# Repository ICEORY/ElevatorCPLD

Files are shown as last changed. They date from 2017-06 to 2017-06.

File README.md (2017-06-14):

## **五层楼的简易电梯控制系统**

### 目录

[TOC]

### 整体方案设计

项目本着“各个击破，各司其职”的指导思想进行设计。各个击破是指将整个电梯控制系统分为各个小模块进行设计，在完成小模块设计之后再进行组合最终实现需要的功能；各司其职指在设计的时候保证每个小模块执行自己要实现的功能，能够正确处理设计范围内的输入。

将整个控制系统根据功能细分为各个小功能模块，主要利用JK触发器74113o以及8-3编码器74148、数值比较器7485等数字模块搭建出系统需要的各个小模块，最后根据各个模块的之间的逻辑联系构建出整个系统。

在使用QuartusII软件搭建各个模块时，每搭建一个功能模块就要对其输入输出逻辑进行仿真，保证其输入输出的波形图满足需要的逻辑功能。当每个模块都能各司其职时，最终搭建整个控制系统才能做到事半功倍，清晰有条理。

根据题目的设计要求，整个电梯控制系统结构图如下所示：

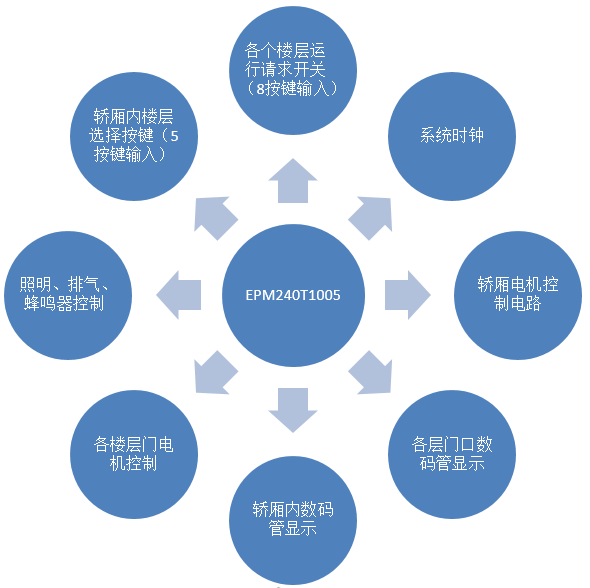
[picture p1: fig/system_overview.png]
system_overview


根据上述功能，将电路分为以下几个模块：

| 模块名称 | 目标实现功能 |
| --- | --- |
| keyinput | 获取单个按键输入，并能够存储按键状态，能够根据外部输入重置按键状态 |
| doormotor | 轿厢门电机，控制开关门动作，进行10ms计时，9s工作周期，其中开关门各一秒，停止7s，具有复位重新计时功能 |
| motion | 20s工作周期，能够根据上下行方向控制三相输出端的输出顺序 |
| timescale | 输入1KHZ时钟信号，进行分频之后输出1HZ,10HZ,100HZ,1KHZ的时钟信号 |
| floorcount  | 输入楼层到达信号时上升沿触发，根据运行方向进行所存储的楼层数的加减，并输出计算结果 |
| nextfloor | 根据运行方向上的按键信息判断是否需要继续运行，判断是否需要开门，判断下次运行方向 |
| otherdevice | 对电梯其他辅助模块如蜂鸣器、排气、照明等设备进行控制 |
| display | 轿厢内、电梯门口的电梯所在楼层信息显示，包括所在楼层，运行方向 |

电梯运行的逻辑如下所示：

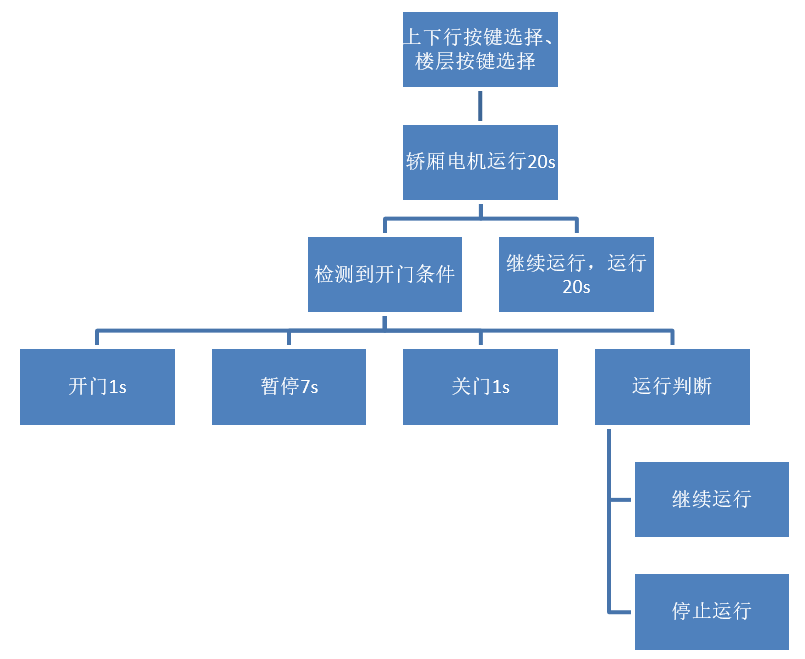
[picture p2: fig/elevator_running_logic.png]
elevator_running_logic


### 电路设计及原理说明

#### 按键电路设计

##### keyinput模块设计

根据功能要求，该模块的应具备以下的输入输出端口：

| input | output |
| ----- | --- |
| KEY | KEYSTATE |
| DONE  | DO |
| CLK | |

在逻辑上应满足：

1. 接收到外界按键信息时，将输出的KEYSTATE强制为1；
2. 当接收到复位指令DONE=1时，将KEYSTATE复位为0，并输入DO信号，用于指示其他模块执行任务；如：用于开门信号；

根据以上要求，使用JK触发器搭建该子模块,真值表如下：

KEYSTATE真值表：

| KEY  | DONE | KEYSTATE | KEYSTATE* |
| ---- | ---- | --- | --- |
| 0 | 0 | 0 | 0 |
| 0 | 0 | 1 | 1 |
| 0 | 1 | 0 | 0 |
| 0 | 1 | 1 | 0 |
| 1 | 0 | 0 | 1 |
| 1 | 0 | 1 | 1 |
| 1 | 1 | 0 | 1 |
| 1 | 1 | 1 | 1 |

DO真值表：

| DONE | KEYSTATE | DO | DO*  |
| ---- | --- | ---- | ---- |
| 0 | 0 | 0 | 0 |
| 0 | 0 | 1 | 0 |
| 0 | 1 | 0 | 0 |
| 0 | 1 | 1 | 0 |
| 1 | 0 | 0 | 0 |
| 1 | 0 | 1 | 1 |
| 1 | 1 | 0 | 1 |
| 1 | 1 | 1 | 1 |

根据计算得到的逻辑关系使用74113搭建出如下电路：

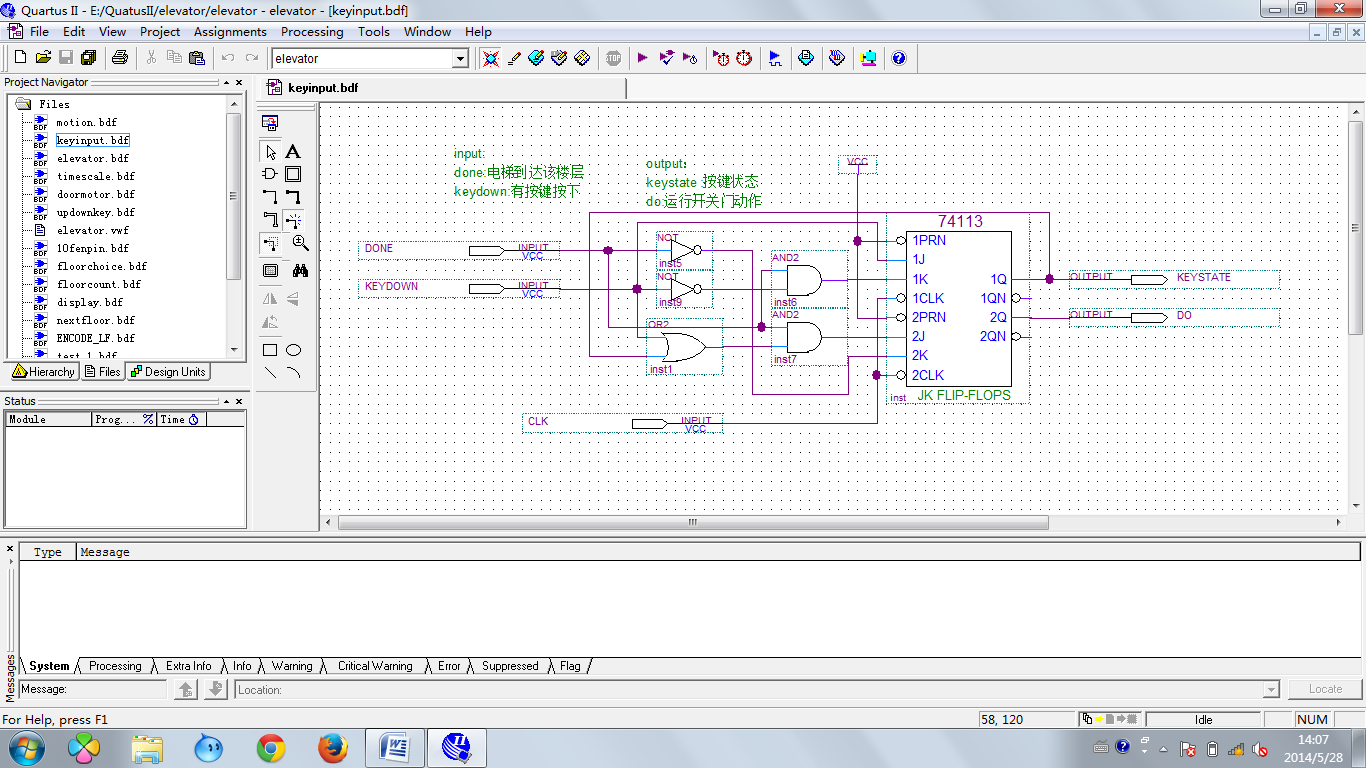
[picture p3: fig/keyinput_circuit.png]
keyinput_circuit


仿真结果如下所示：

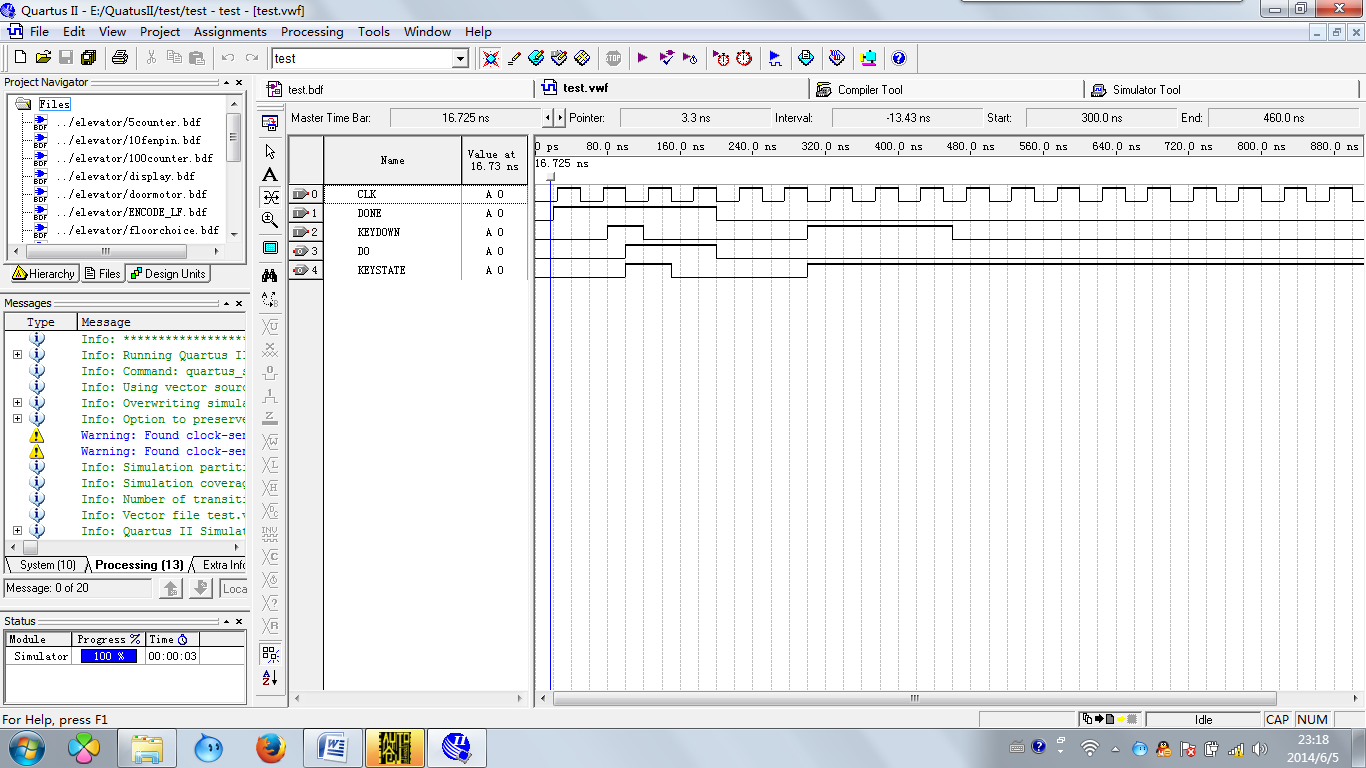
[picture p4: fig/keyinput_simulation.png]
keyinput_simulation


##### updownkey模块设计

构建完单个按键的输入电路之后利用该模块进一步构建电梯上下行选择按键输入；该模块由由八个keyinput单元构成；其输入输出如下表所示：

| input | output |
| --- | --- |
| UP1~UP4 | KEYSTATE1~KEYSTATE8 |
| DOWN2~DOWN5 | DOOR`~DOOR5 |
| CLK | |
| FLOORA~FLOORC | |
| U/D | |
| ARRIVE | |

根据五层电梯的实际情况，一楼只有上行按钮，五楼只有下行按钮，中间三层具有上下行按钮，共八个按键输入，输出控制五层楼的轿厢外门电机，故具有五个门控制输出，八个按键状态输出。

使用74138三-八译码器将输入的所在楼层信息译成八个按键状态的控制信息，其逻辑真值表如下：

| FLOORC | FLOORB | FLOORA | Y0 | Y1 | Y2 | Y3 | Y4 | Y5 | Y6 | Y7 |
| --- | --- | --- | ---- | ---- | ---- | ---- | ---- | ---- | ---- | ---- |
| 0 | 0 | 0 | 0 | 1 | 1 | 1 | 1 | 1 | 1 | 1 |
| 0 | 0 | 1 | 1 | 0 | 1 | 1 | 1 | 1 | 1 | 1 |
| 0 | 1 | 0 | 1 | 1 | 0 | 1 | 1 | 1 | 1 | 1 |
| 0 | 1 | 1 | 1 | 1 | 1 | 0 | 1 | 1 | 1 | 1 |
| 1 | 0 | 0 | 1 | 1 | 1 | 1 | 0 | 1 | 1 | 1 |
| 1 | 0 | 1 | 1 | 1 | 1 | 1 | 1 | 0 | 1 | 1 |
| 1 | 1 | 0 | 1 | 1 | 1 | 1 | 1 | 1 | 0 | 1 |
| 1 | 1 | 1 | 1 | 1 | 1 | 1 | 1 | 1 | 1 | 0 |

各个按键与输入的ARRIVE、U/D逻辑关系满足：（以Y2为例）

| ARRIVE | U/D  | Y2 | DONE |
| --- | ---- | ---- | ---- |
| 0 | 0 | 0 | 0 |
| 0 | 0 | 1 | 0 |
| 0 | 1 | 0 | 0 |
| 0 | 1 | 1 | 0 |
| 1 | 0 | 0 | 0 |
| 1 | 0 | 1 | 0 |
| 1 | 1 | 0 | 1 |
| 1 | 1 | 1 | 0 |

该模块的输出DOOR逻辑上等于各个按键子模块输出的DO

电路如下所示：

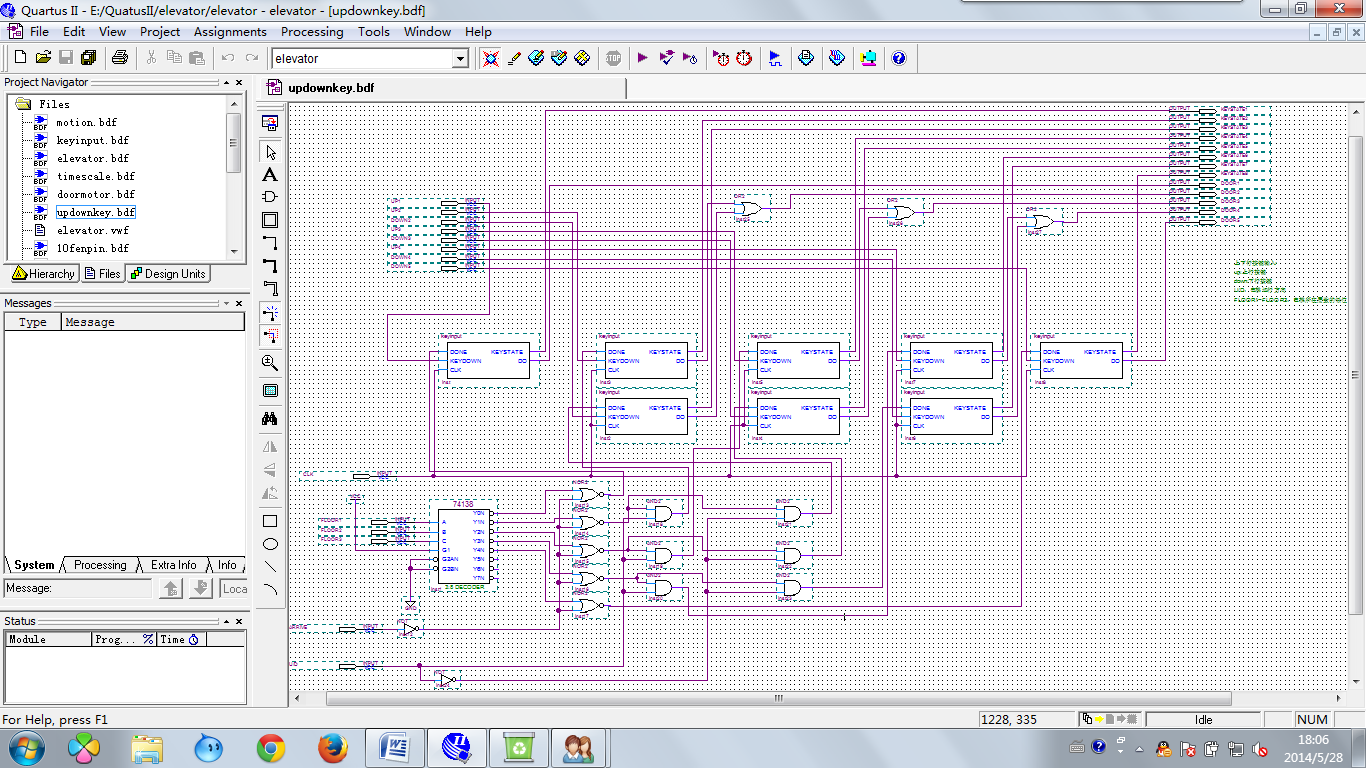
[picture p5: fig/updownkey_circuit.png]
updownkey_circuit


该模块整体仿真波形如下：

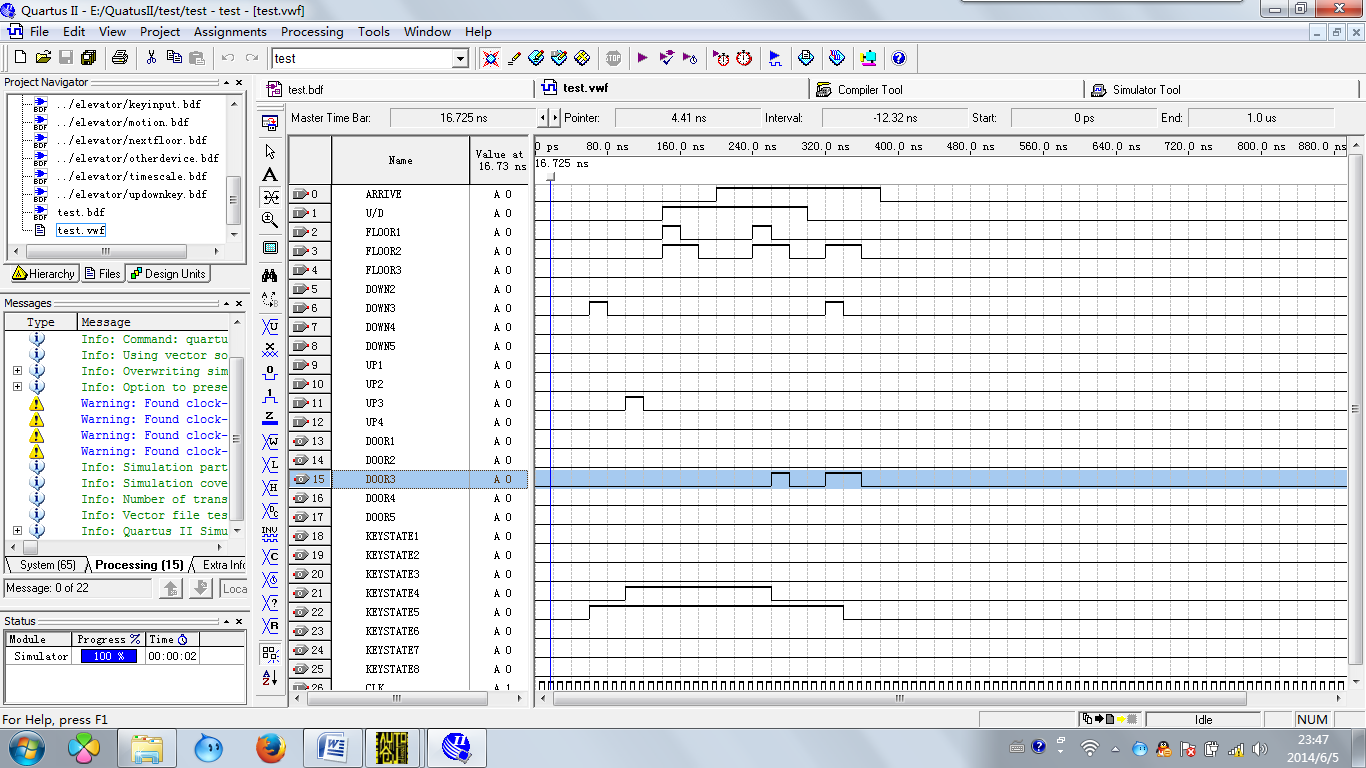
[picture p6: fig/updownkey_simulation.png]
updownkey_simulation


图中以第三层的上下行按键为例，在电梯没有到达三层时按下上下行按键，可见电梯不会进行开关门动作，并且将按键状态存储。在电梯到达三层时，由于电梯运行方向为上行（U/D=1），此时只判断上行方向的按键（KEYSTATE4），进行开门动作并将按键状态复位。电梯在三层的时候若运行方向改变为下行（U/D=0），此时进行开门动作，但由于同时在三层再次按下下行键故按键的按下状态一直持续到按键松开为止而，开门动作一直持续到楼层发生变化。可见，该模块设计符合实际电梯运行的逻辑。

##### floorchoice模块设计

电梯轿厢内的楼层选择仍选择用上述的按键模块，电路逻辑与updownkey模块的设计类似，其中keyinput模块满足：

1. KEYDOWN=KEY；
2. DONE=Y’ARRIVE’。

Floorchoice模块同时控制轿厢门电机的运动：

DOOR=DO1+D2+DO3+DO4+DO5;

电路设计如下所示：

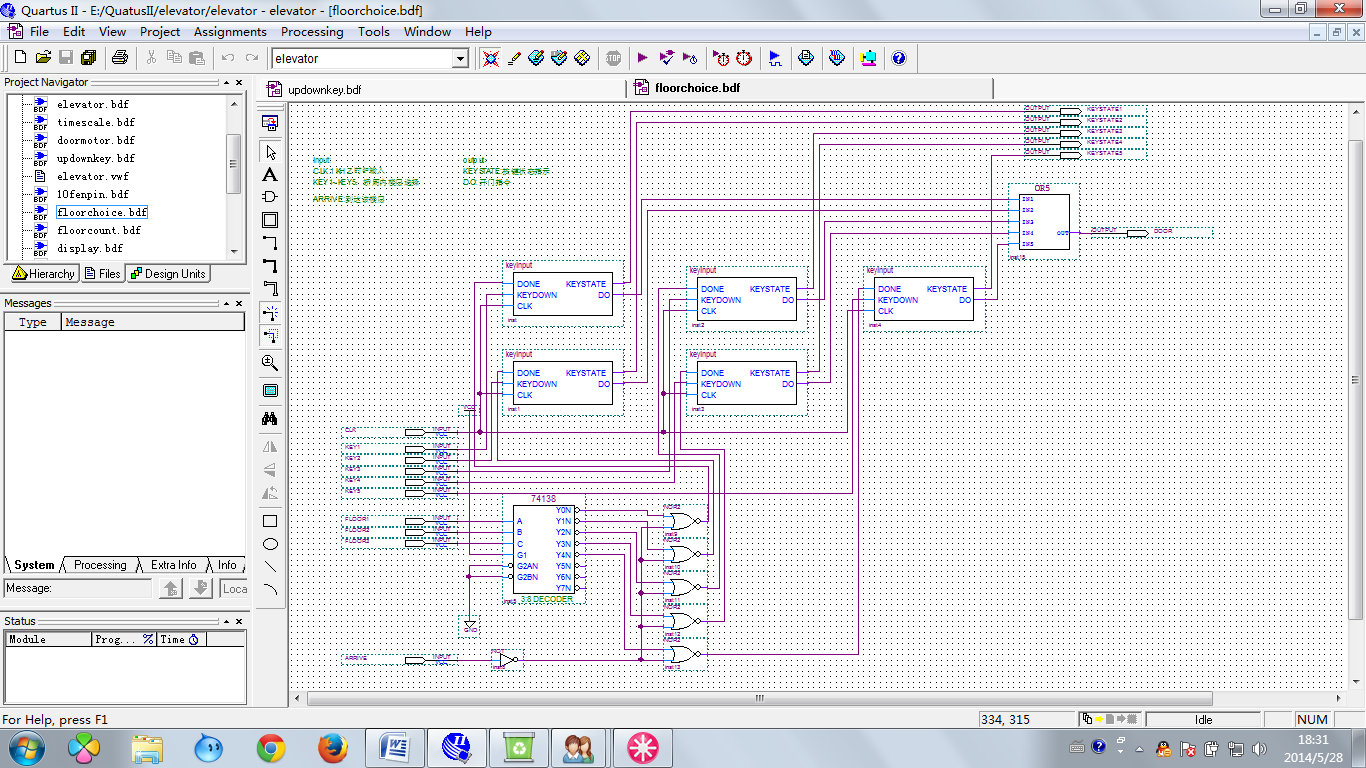
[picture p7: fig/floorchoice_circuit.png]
floorchoice_circuit


该模块整体仿真波形如下：

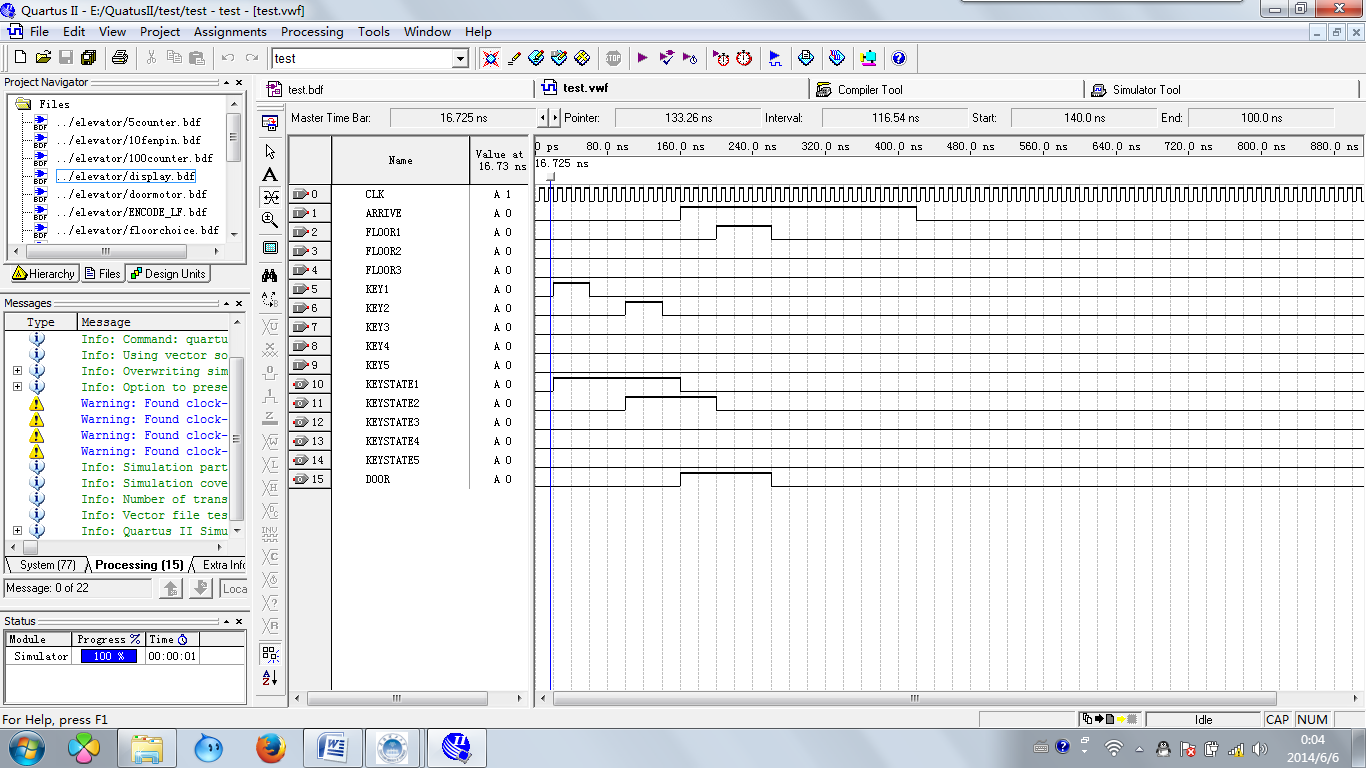
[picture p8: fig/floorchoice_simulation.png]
floorchoice_simulation


图中以一层与二层的按键选择为例，在电梯到达之前，根据输入将按键状态进行保存。在电梯到达相应楼层时进行开门动作并将对应按键复位。

#### 时钟电路设计

##### 10fenpin 模块设计

由于该电梯输入时钟频率为10kHz，故设计一个十分频电路将输入的时钟进行十分频，用于输出1Hz,10Hz,100Hz,1kHz等频率的时钟用于各个模块工作需要。使用74190十进制计数器作为分频核心模块，其逻辑真值表如下：

| QD | QC | QB | QA | CO |
| ---- | ---- | ---- | ---- | ---- |
| 0 | 0 | 0 | 0 | 0 |
| 0 | 0 | 0 | 1 | 0 |
| 0 | 0 | 1 | 0 | 0 |
| 0 | 0 | 1 | 1 | 0 |
| 0 | 1 | 0 | 0 | 0 |
| 0 | 1 | 0 | 1 | 1 |
| 0 | 1 | 1 | 0 | 1 |
| 0 | 1 | 1 | 1 | 1 |
| 1 | 0 | 0 | 0 | 1 |
| 1 | 0 | 0 | 1 | 1 |

电路设计如下所示：

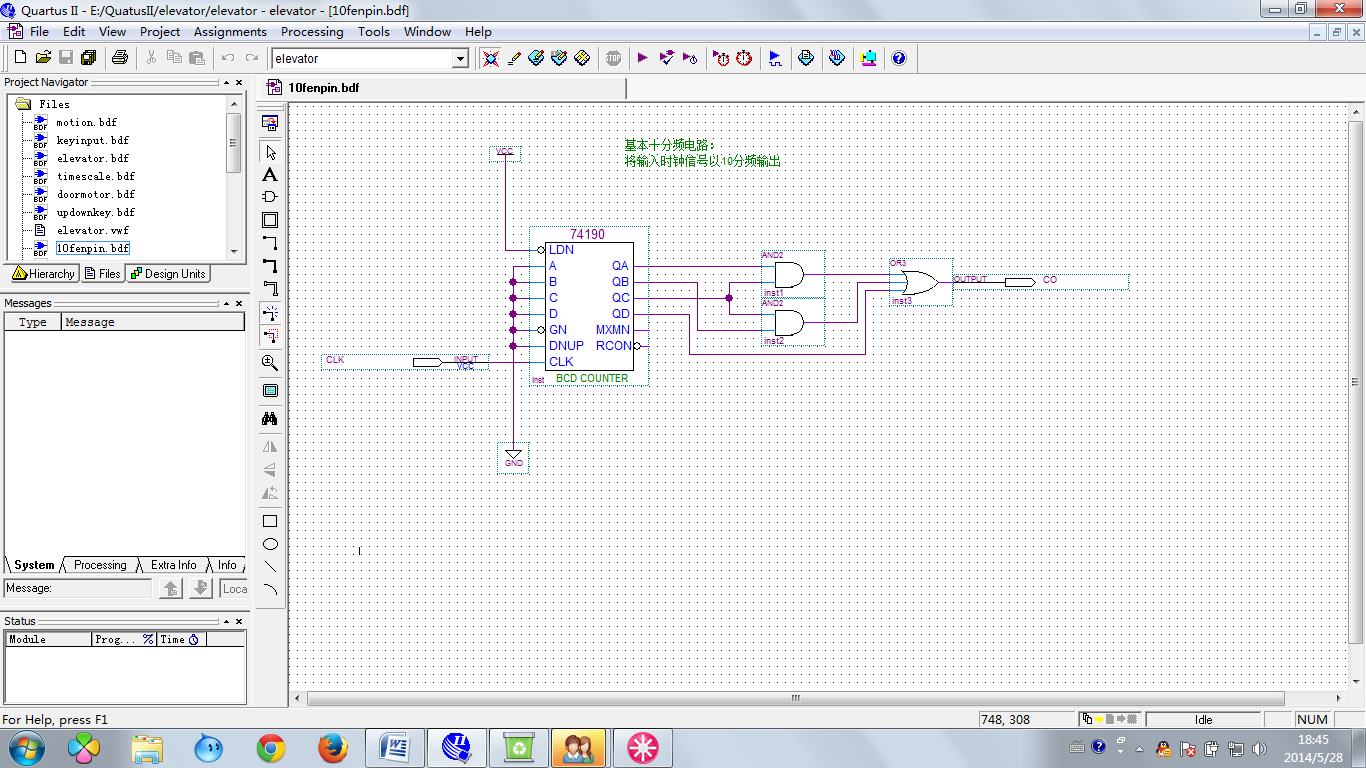
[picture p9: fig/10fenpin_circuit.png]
10fenpin_circuit


##### timescale模块设计

使用上述10fenpin模块构建多频率输出的timescale模块用于提供各个模块的时钟信号。模块原理同异步计数器的设计原理，电路图如下所示：

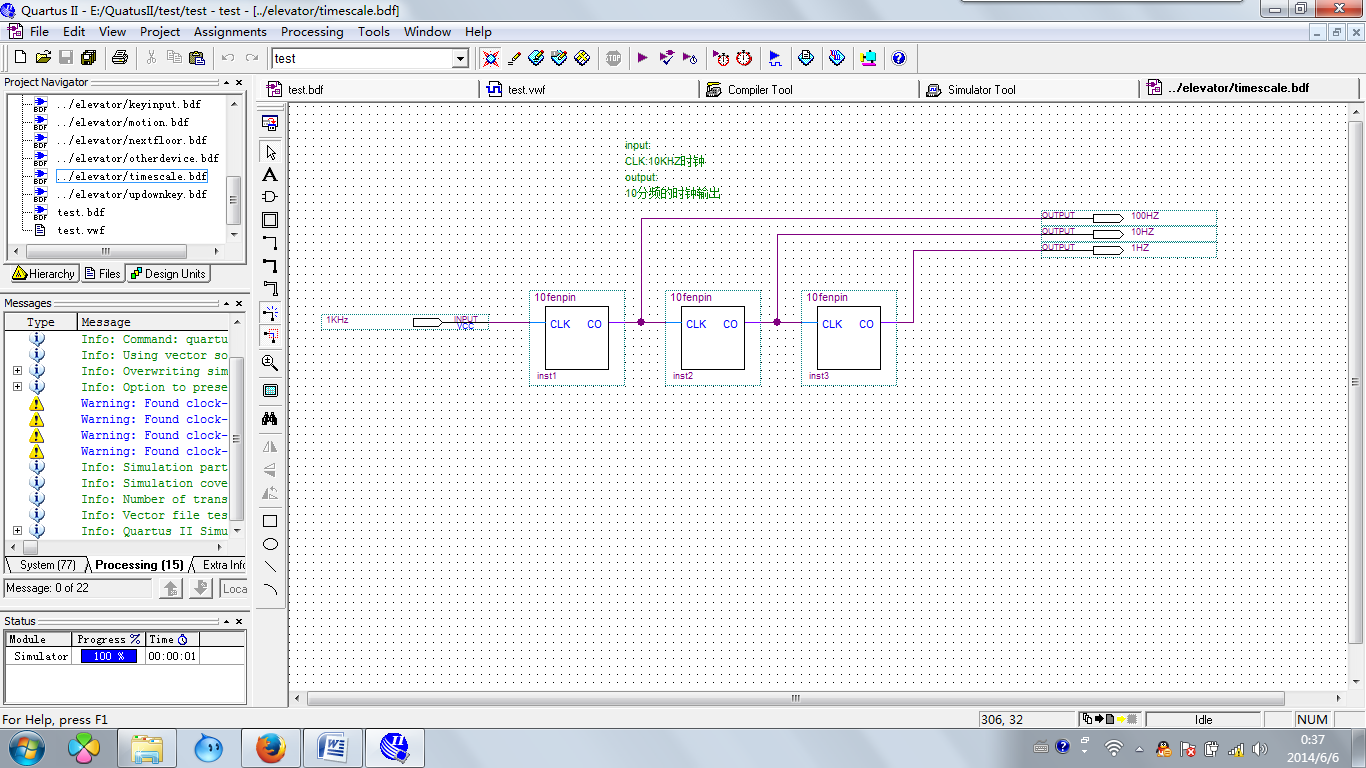
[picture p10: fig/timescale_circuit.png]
timescale_circuit


#### 系统决策电路设计

##### ENCODE_LE模块设计

由于8-三编码器74148是高位优先编码器，根据电梯上下楼层排序的需要，在下行时需要对输入进行低位优先编码，故以编码器74148为核心设计一个五-三低位优先编码器；设计原理是先将输入进行倒序处理,模块输入与74148芯片接口如下：

| IN4  | 0N |
| ---- | ---- |
| IN3  | 1N |
| IN2  | 2N |
| IN1  | 3N |
| IN0  | 4N |

根据上表可以对输入的低位进行优先编码，但由此导致了输出与输入的错位，使用门电路对输出进行校正，使输入IN0=1时，输出编码A2=0;A1=0;A3=0;真值表如下所示：

| A2N  | A1N  | A0N  | A2 | A1 | A0 |
| ---- | ---- | ---- | ---- | ---- | ---- |
| 1 | 1 | 1 | 1 | 0 | 0 |
| 1 | 1 | 0 | 0 | 1 | 1 |
| 1 | 0 | 1 | 0 | 1 | 0 |
| 1 | 0 | 0 | 0 | 0 | 1 |
| 0 | 1 | 1 | 0 | 0 | 0 |

此外当外界没有输入时，A2=1，A1=1;A0=1;

电路设计如下所示：

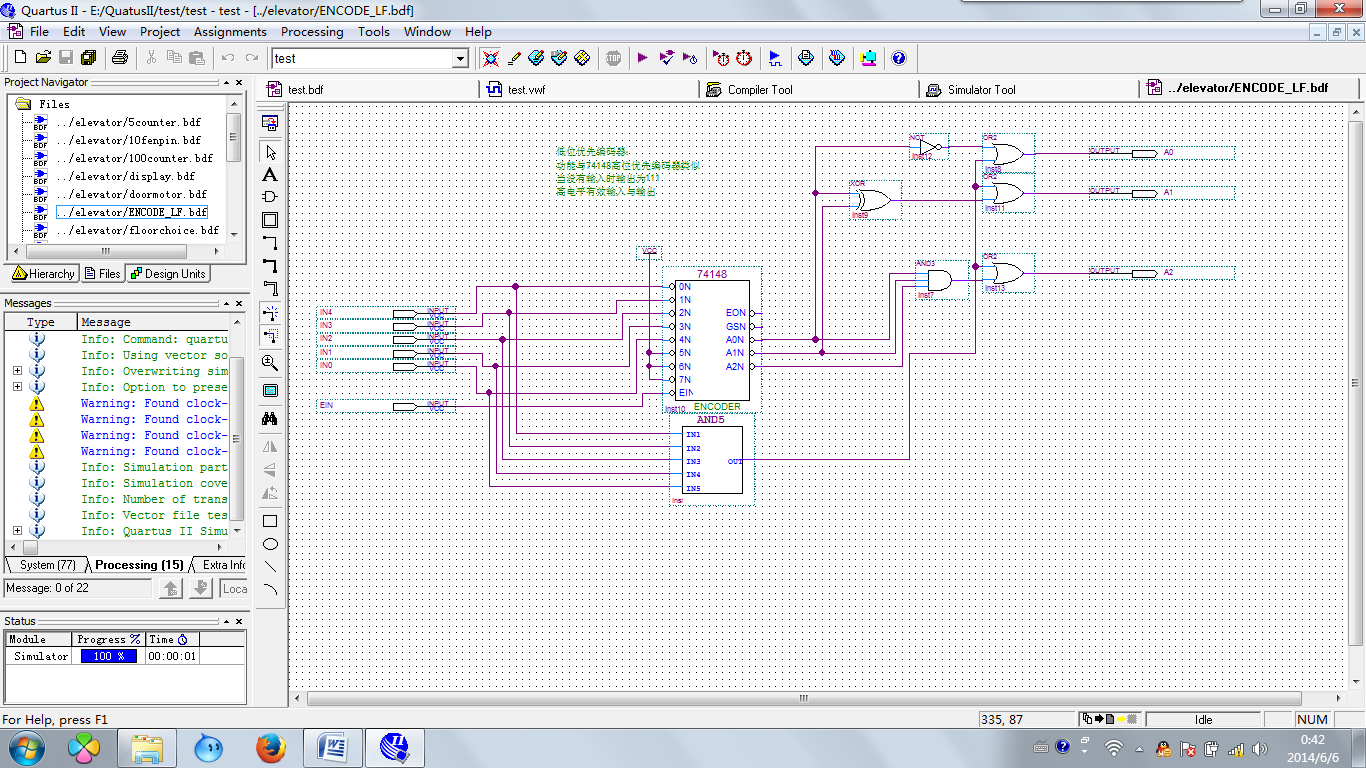
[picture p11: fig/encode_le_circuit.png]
encode_le_circuit


仿真波形如下图所示：

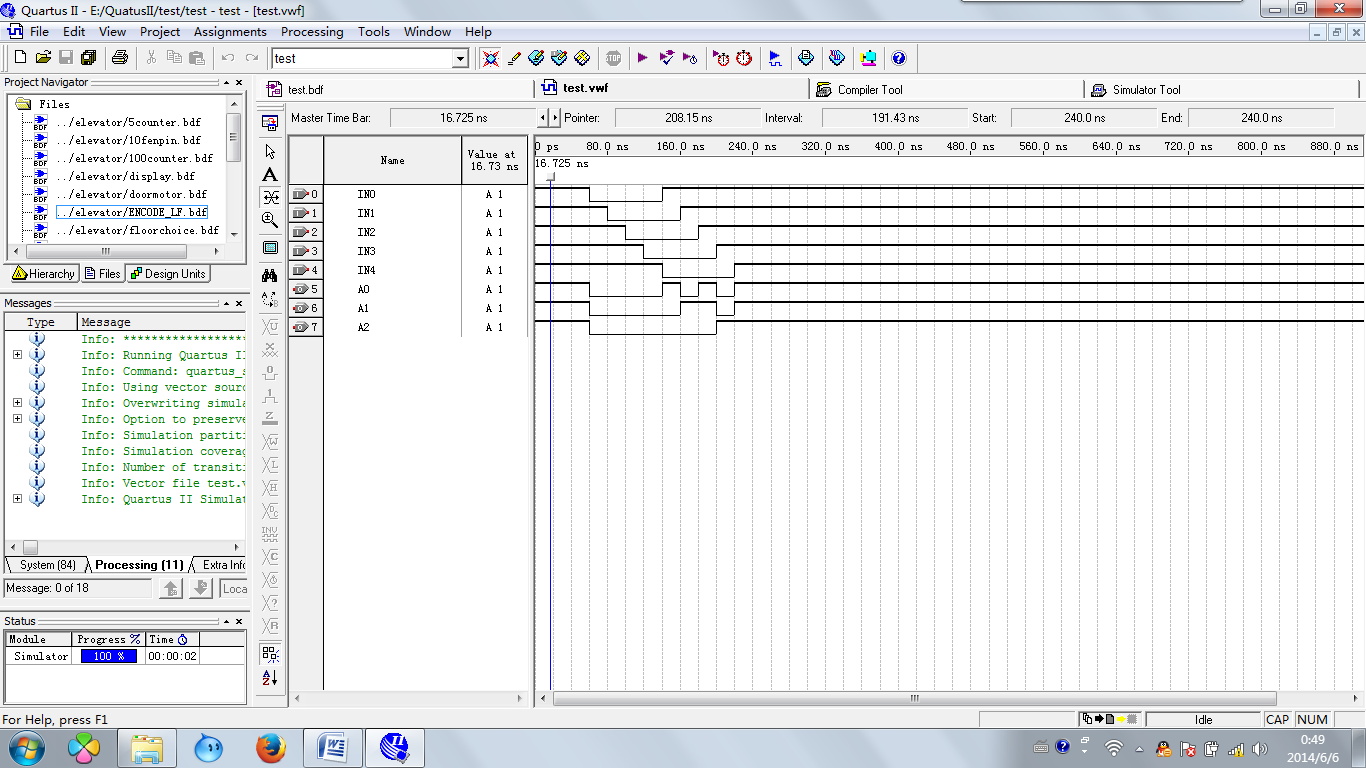
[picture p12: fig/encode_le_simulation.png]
encode_le_simulation


##### nextfloor模块设计

使用上述构建的ENCODE_LF模块与高位优先编码器74148搭建电梯的核心决策模块nextfloor，该模块根据按键的输入以及当前电梯所在的楼层输出电梯即将进行的动作，输入输出列表如下：

| KEYSTATE1~KEYSTATE8(上下行按键选择) | OPEN（开门信号）  |
| --- | --- |
| CHOICE1~CHOICE5（目标楼层选择） | RUN（电梯运行信号） |
| FLOORA~FLOORC（当前电梯的位置） | DIR（电梯运行方向） |
| CLK | |

使用高位优先编码器对输入的KEYSTATE以及CHOICE进行高位优先编码，输出其中的按键的最大值并使用数值比较器7485将键值与当前电梯所处的楼层进行比较决定电梯是否继续运行，设U=1表示电梯上行方向上有按键按下，且键值大于当前楼层；U=0 表示电梯上行方向没有键值大于当前楼层的按键按下；设D=1 表示电梯下行方向有键值小于当前楼层的按键按下；D=0表示电梯下行方向没有键值小于当前楼层的按键按下；电梯是否继续运行的判断值RUN应该满足RUN=U+D;

而电梯运行的方向DIR与U/D关系的真值表如下：

| U | D | DIR  | DIR* |
| ---- | ---- | ---- | ---- |
| 0 | 0 | 0 | X |
| 0 | 0 | 1 | X |
| 0 | 1 | 0 | 0 |
| 0 | 1 | 1 | 0 |
| 1 | 0 | 0 | 1 |
| 1 | 0 | 1 | 1 |
| 1 | 1 | 0 | 0 |
| 1 | 1 | 1 | 1 |

当U/D均为0时需要对电梯的运行方向进行进一步的判断，U/D为零一般出现在第一次按下上下行按键时出现，此时电梯位置与按键所在楼层一致且没有其他按键按下，故设UE=1表示电梯所在位置有上行方向的按键按下且没有其他按键选择；DE=1表示电梯所在位置有下行方向的按键按下且没有其他按键选择；

此时RUN=0,DIR与UE/DE的关系如下：

| UE | DE | DIR  | DIR* |
| ---- | ---- | ---- | ---- |
| 0 | 0 | 0 | 0 |
| 0 | 0 | 1 | 1 |
| 0 | 1 | 0 | 0 |
| 0 | 1 | 1 | 0 |
| 1 | 0 | 0 | 1 |
| 1 | 0 | 1 | 1 |
| 1 | 1 | 0 | 0 |
| 1 | 1 | 1 | 1 |

开门信号OPEN=RUN’DE

电路设计如下图所示：

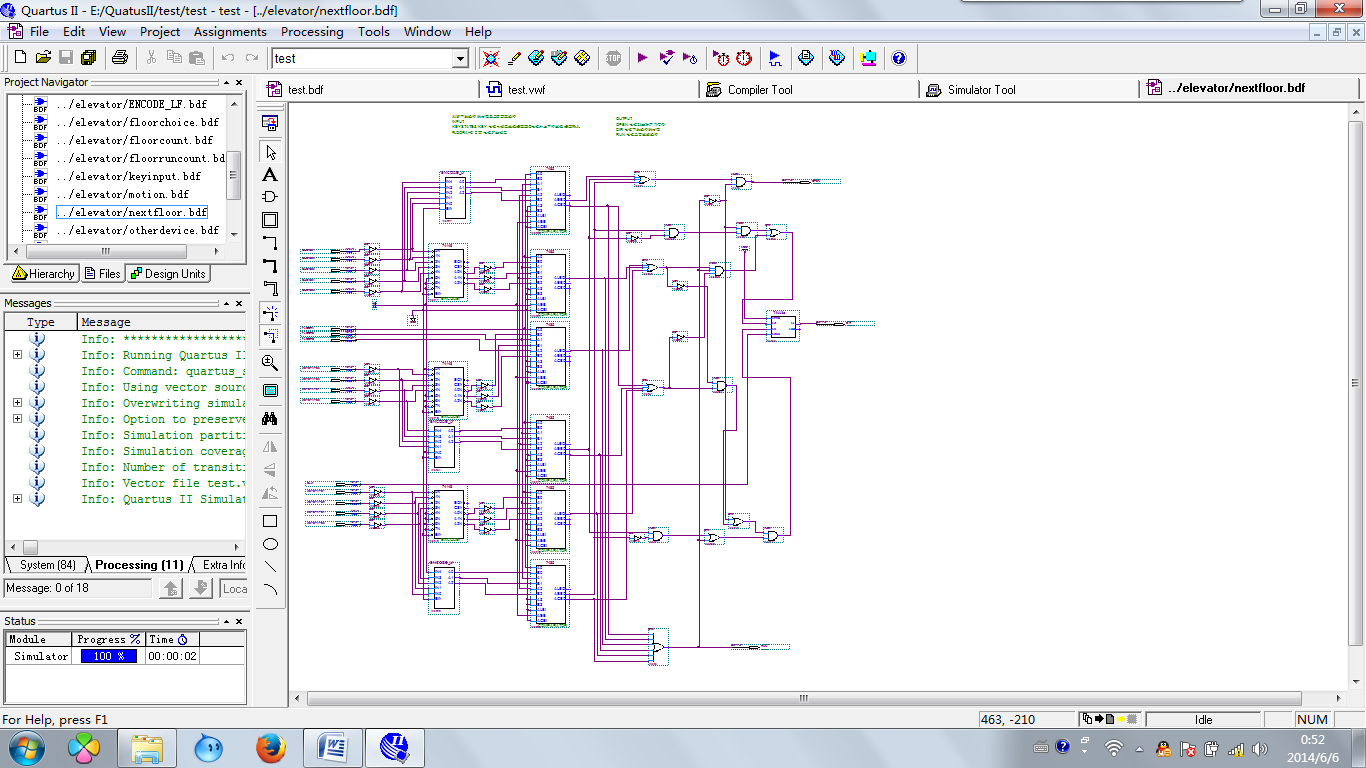
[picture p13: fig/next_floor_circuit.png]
next_floor_circuit


#### 电机电路设计

##### motion模块设计

由于本课题所使用的轿厢电机设定为四线三相步进电机，故需要根据输入的运行方向以及开门信号输出相应的三相电压的变化，电机正转时运行逻辑为A-B-C-A,反转时逻辑为A-C-B-A。使用双JK触发器74113构建三进制触发器，其计数顺序为00-01-10-00。

Q2\*Q1\*的卡诺图如下所示：

| Q2  Q1 | 0 | 1 |
| --- | ---- | ---- |
| 0 | 01 | 10 |
| 1 | 00 | XX |

    电机控制输出的逻辑真值表如下所示：

| RUN  | U/D  | Q2Q1 | A | B | C |
| ---- | ---- | ---- | ---- | ---- | ---- |
| 0 | X | X | 0 | 0 | 0 |
| 1 | 0 | 00 | 1 | 0 | 0 |
| 1 | 0 | 01 | 0 | 1 | 0 |
| 1 | 0 | 11 | 0 | 0 | 1 |
| 1 | 1 | 00 | 1 | 0 | 0 |
| 1 | 1 | 01 | 0 | 0 | 1 |
| 1 | 1 | 10 | 0 | 1 | 0 |

此外根据题目要求，每两个楼层之间电机运行时间为20s，故使用十进制计数器74190与二进制计数器74161构成二十进制计数器。

电路设计如下所示：

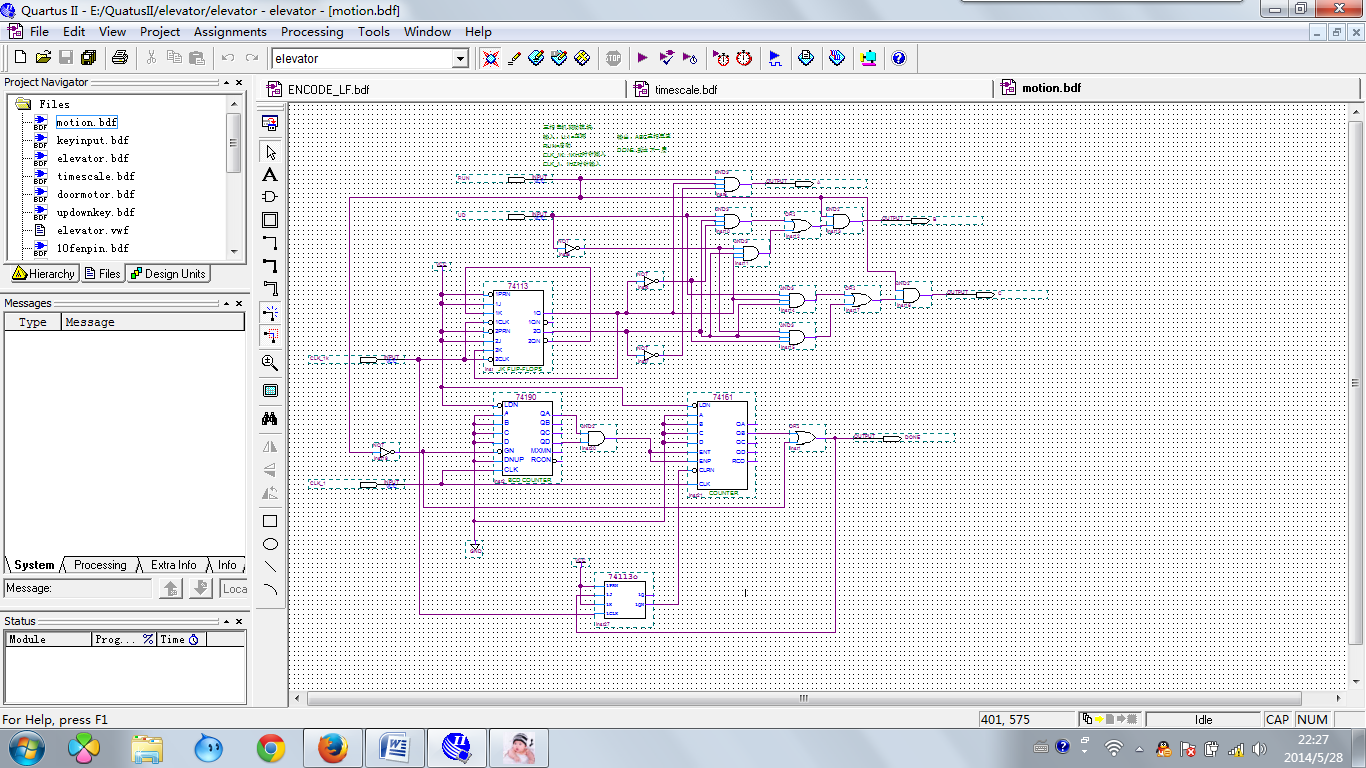
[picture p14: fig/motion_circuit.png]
motion_circuit


##### doormotor模块设计

在电梯到达目标楼层之后，电梯需要控制门电机依次执行以下动作：开门1s—停止7s—关门1s；其中在关门1s时间内根据电梯实际运行方向判断相应的按键输入，如上行时上行按键按下或者下行时下行按键按下则门重新打开，或者在门关闭时遇到障碍物也重新打开门。由分析可知，以上三种门重新打开的情况只需要归结为一个复位开门的指令给门电机控制模块即可。

由于本课题的门电机选择直流电机，故只需要输出MOTOR1/MOTOR2控制电机的正反转。使用三个74161十六进制计数器搭建900进制计数器，输入100Hz时钟信号控制。在0s时启动MOTOR1，关闭MOTOR2，此时直流电机正转，在1s时关闭MOTOR1，同时保持MOTOR2关闭，此时直流电机不转，在8s时保持MOTOR1关闭，启动MOTOR2，此时直流电机反转，9s时关闭MOTOR2，同时输出电机关门完成信号。****

电路逻辑真值表如下：

| RUN  | Q9~Q0 | MOTOR2  MOTOR1 | DONE |
| ---- | --- | --- | ---- |
| 0 | XXXXXXXXXX | 00 | 1 |
| 1 | 0000000000 | 01 | 0 |
| 1 | 0001100100 | 00 | 0 |
| 1 | 1100100000 | 10 | 0 |
| 1 | 1110000100 | 00 | 1 |

电机运行复位，即计数清零端CLRN’真值表如下：

| RUN  | MOTOR2 | RESET | CLRN |
| ---- | --- | ----- | ---- |
| 0 | X | X | 0 |
| 1 | 0 | X | 1 |
| 1 | 1 | 0 | 1 |
| 1 | 1 | 1 | 0 |

则电路设计如下图所示：

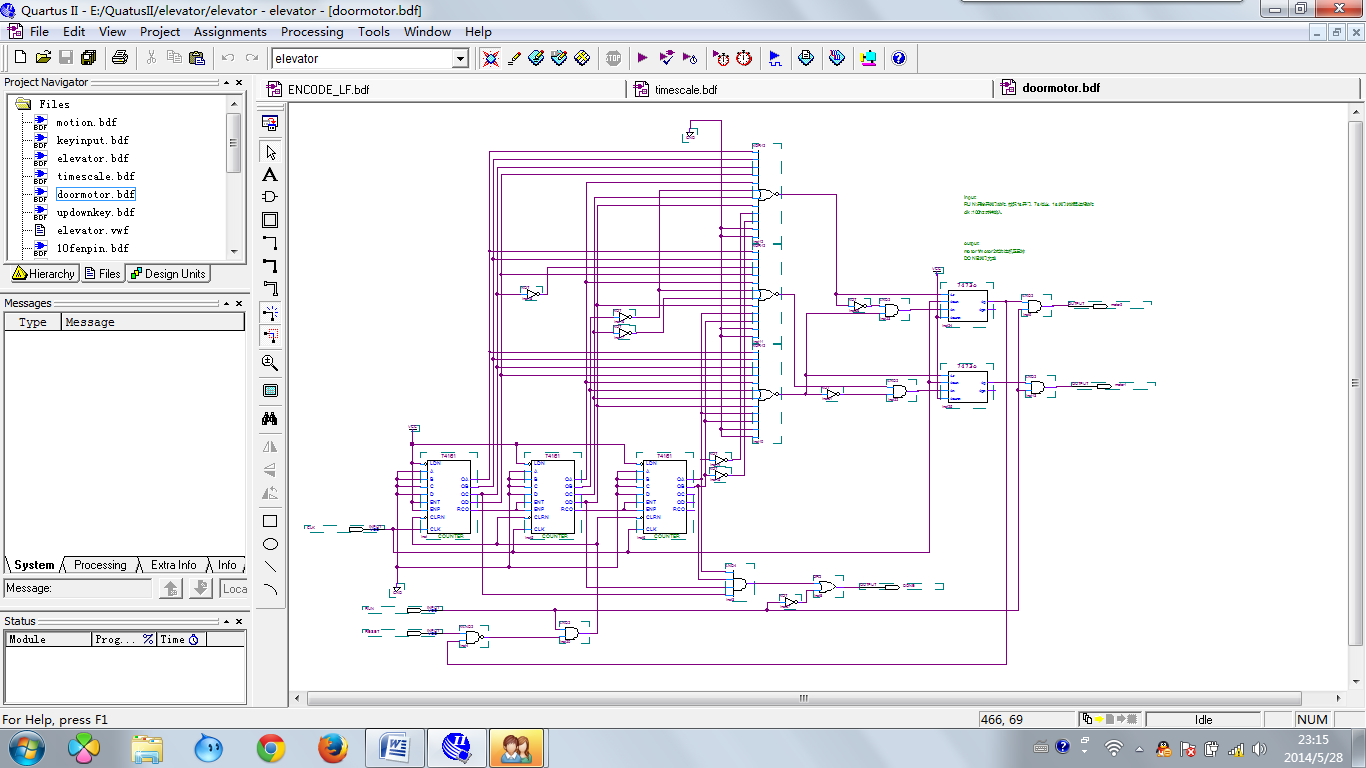
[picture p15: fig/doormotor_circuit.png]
doormotor_circuit


#### 楼层计数电路设计

##### 100counter模块设计

根据题目要求需要对各个楼层进行运行次数计数，考虑到运行次数可能比较多，故采用100进制计数模块，该模块是由两个74190十进制计数器构成的异步计数器，电路原理图如下所示：

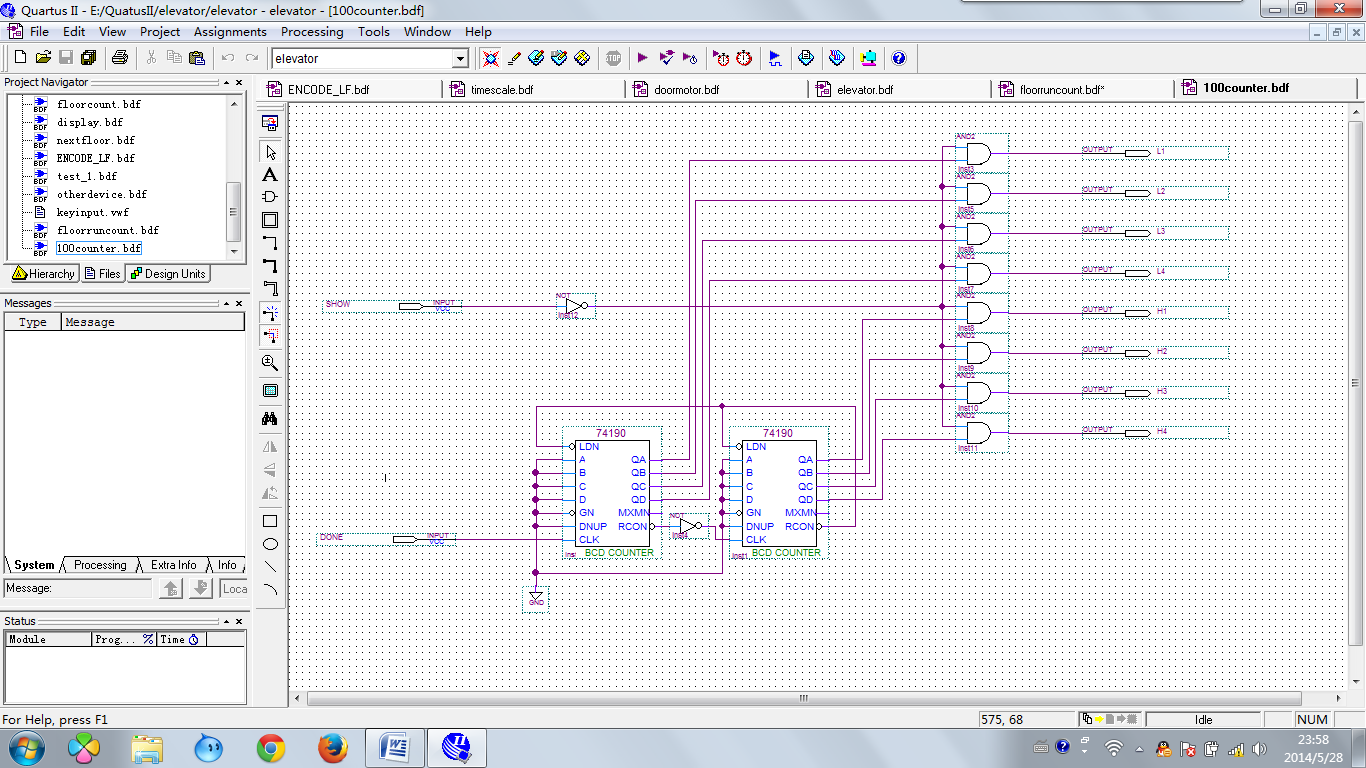
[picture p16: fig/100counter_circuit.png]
100counter_circuit


##### 5counter模块设计

楼层计数时为了节省数码管显示模块的数量，故增加对计数显示的选择按键，每按下一次按键显示的目标楼层自加1，从而实现用同一个对不同楼层计数的显示。由于该课题针对5层楼的电梯设计，故计数选择也是5进制的。为了节省芯片内部模块的资源，故设计该5进制模块用于计数选择。

电路设计如下：

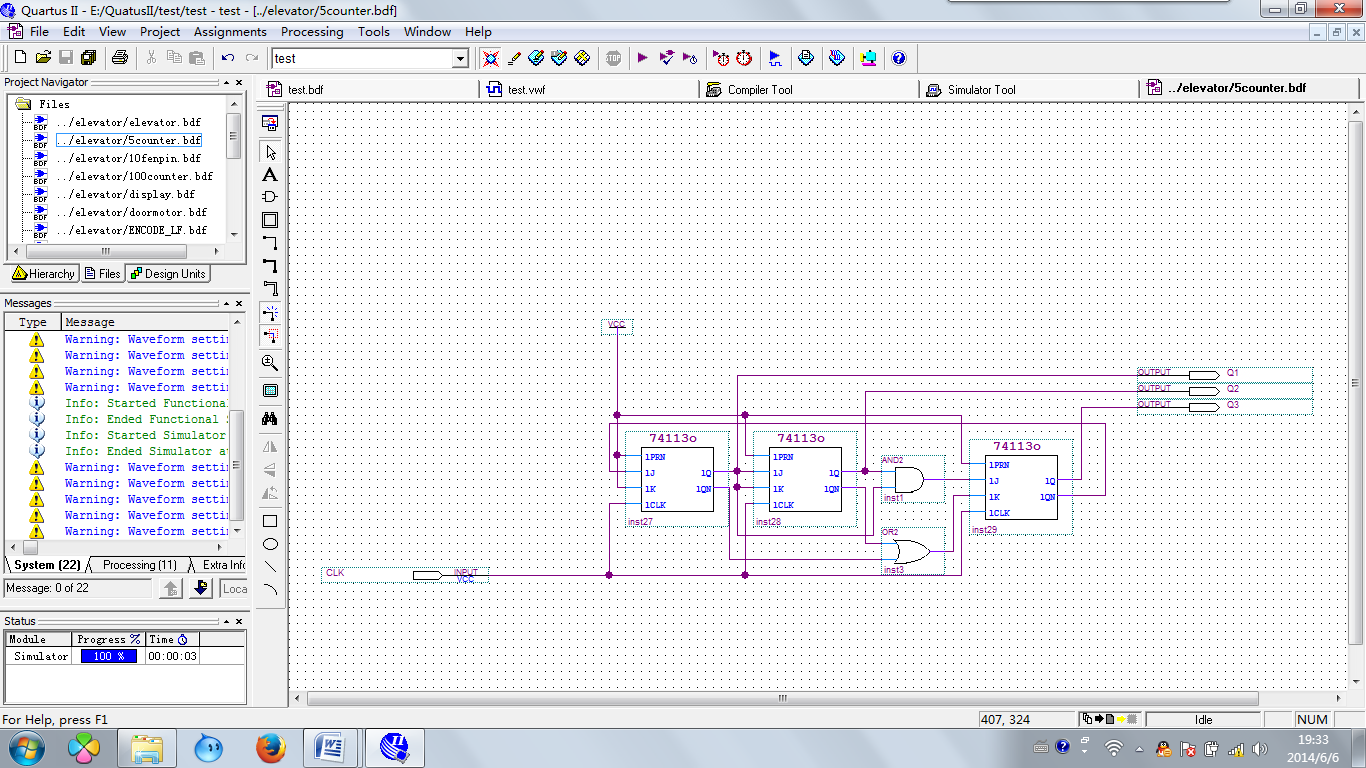
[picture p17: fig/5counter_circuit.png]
5counter_circuit


仿真波形如下：

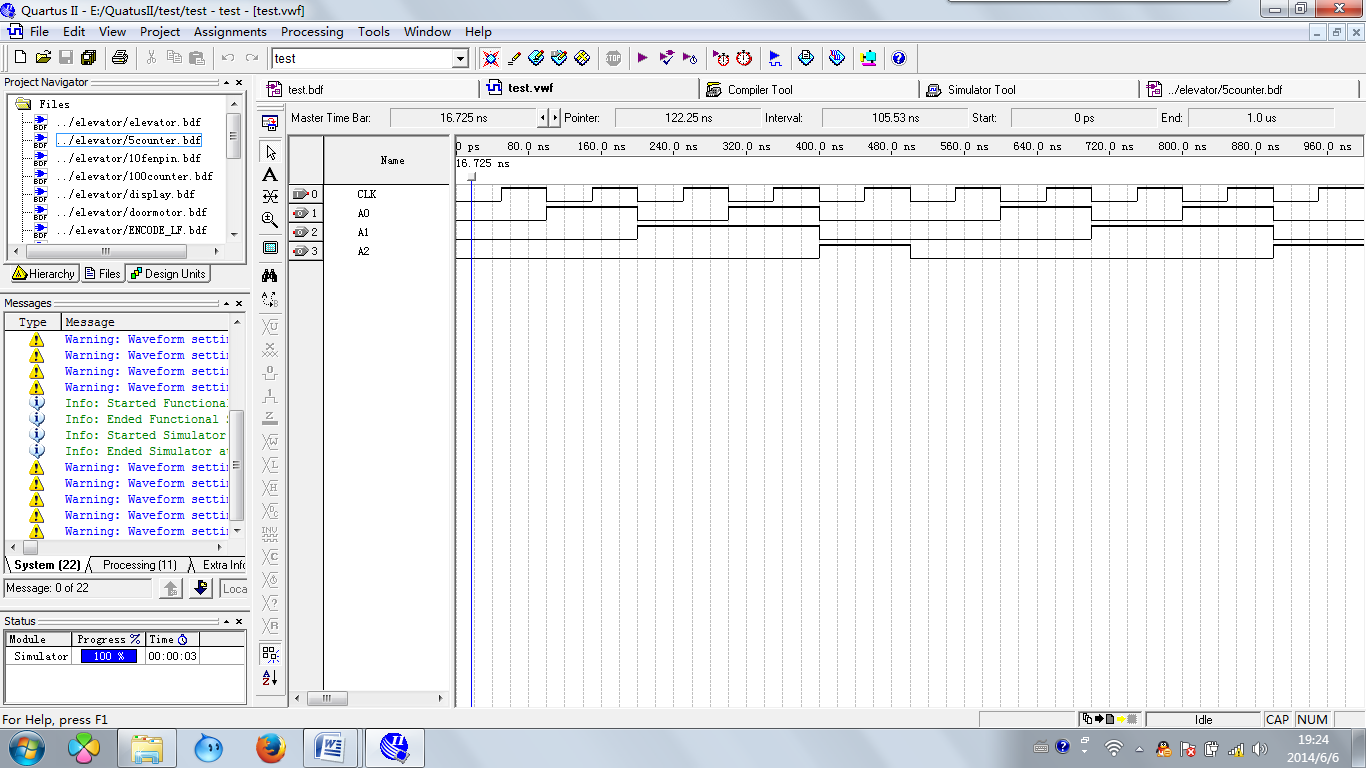
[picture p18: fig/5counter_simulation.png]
5counter_simulation


##### floorruncount模块设计

使用上述100进制计数器搭建每个楼层的运行次数计数模块，输入输出信号列表如下：

| input | output |
| --- | --- |
| FLOORA~FLOORC | FHLED-楼层计数十位显示 |
| DONE | FLLED-楼层计数个位显示 |
| KEYINPUT | CLED-按键选择楼层显示  |

通过三八译码器将输入楼层信号译成五个楼层的选择信号，当DONE=1时该楼层计数增加1；设计原理updownkey模块类似。电路原理如下所示：

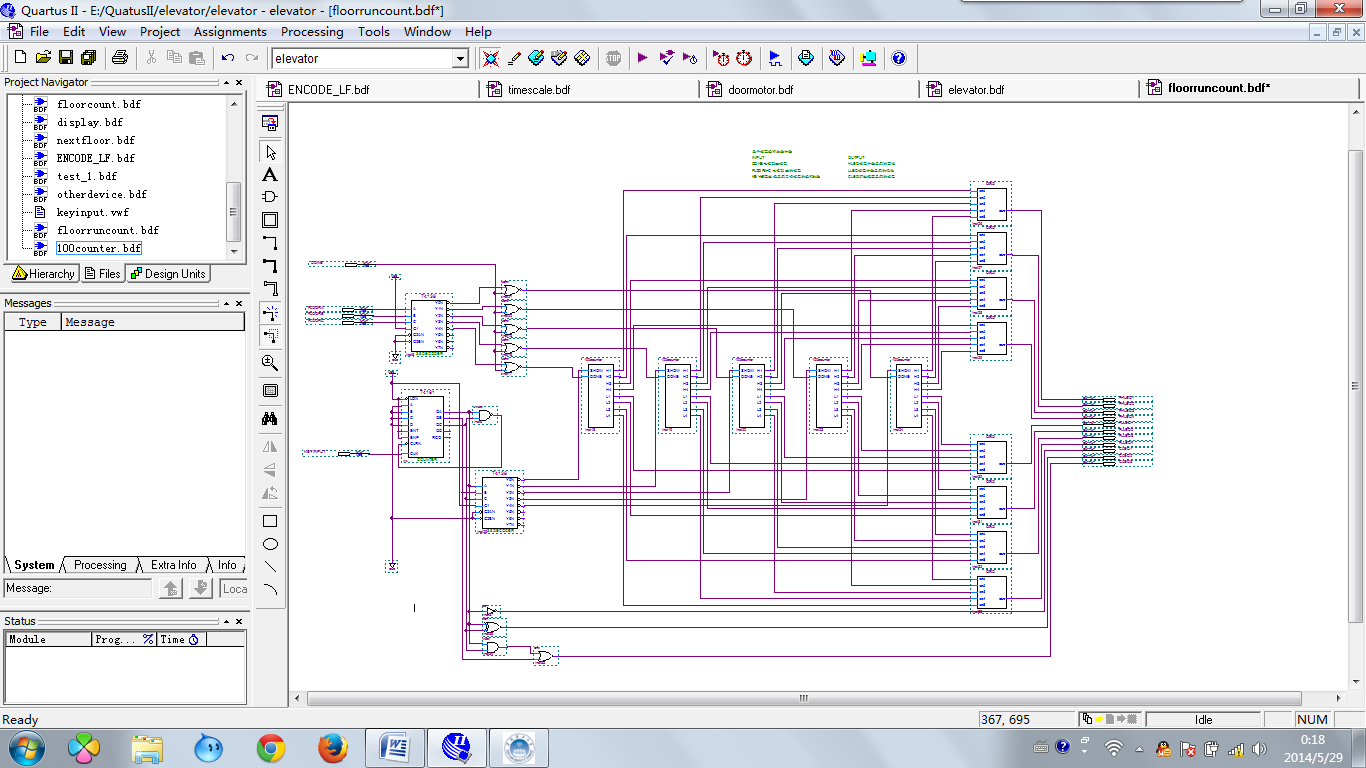
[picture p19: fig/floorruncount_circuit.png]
floorruncount_circuit


#### 排气、照明、蜂鸣器电路设计

##### otherdevice模块设计

将题目要求的其他附属硬件要求整合在该模块中。该模块主要实现对电梯的照明排气、蜂鸣器的控制。根据题目要求可知蜂鸣器在电梯到达目标楼层时响起提示，在本设计中设置为响0.5s，故使用三个JK触发器构建满足以下真值表条件的计数器。

| DONE | Q2Q1Q0 | Q2*Q1*Q0* | BEE  |
| ---- | --- | --- | ---- |
| 1 | XXX | 000 | 0 |
| 0 | 000 | 001 | 1 |
| 0 | 001 | 010 | 1 |
| 0 | 010 | 011 | 1 |
| 0 | 100 | 101 | 1 |
| 0 | 101 | 110 | 1 |
| 0 | 110 | 110 | 0 |

BEE为蜂鸣器的总控制标志，与输入的FLOORA~FLOORC楼层信号配合决定各个楼层蜂鸣器的状态。

电路设计如下所示：

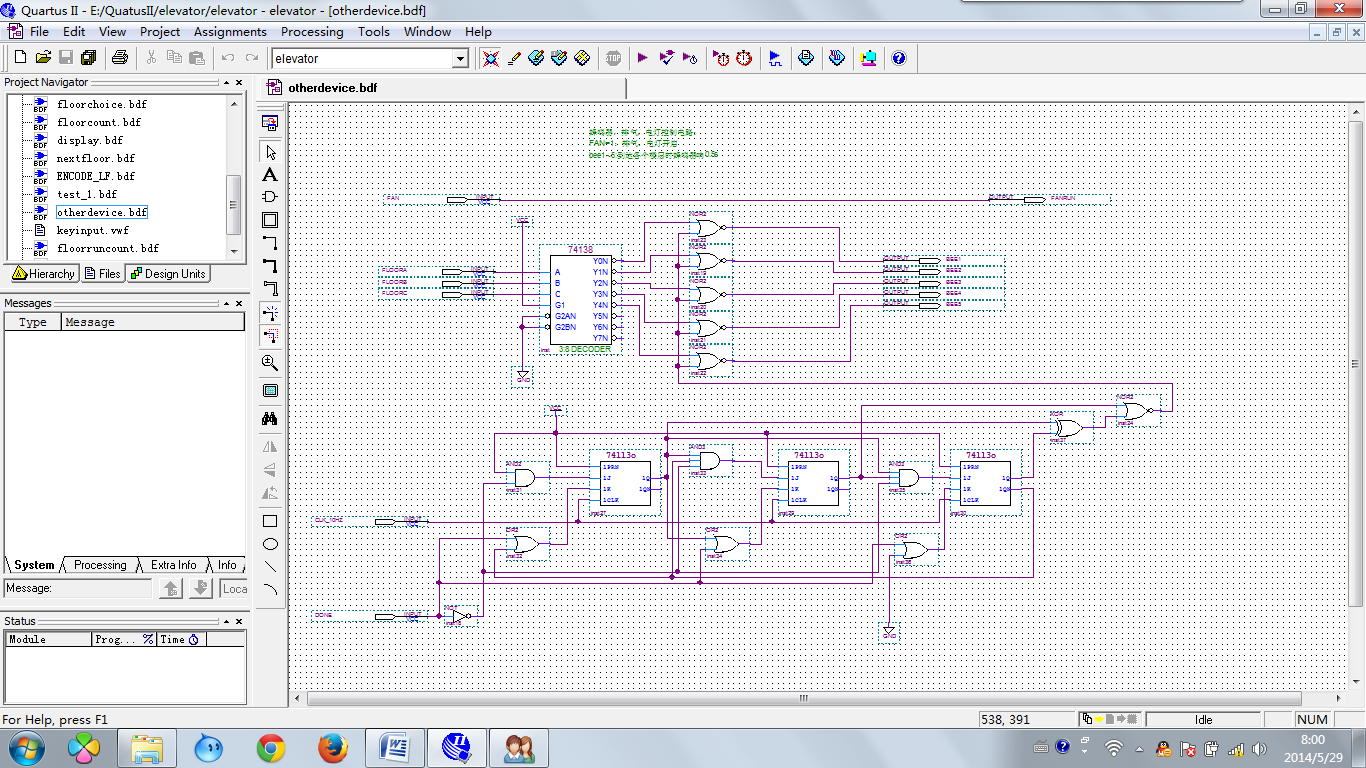
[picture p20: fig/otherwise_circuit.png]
otherwise_circuit


#### 数码管显示电路设计

##### display模块设计

根据题目要求，设计该模块用于轿厢内部以及电梯门外部的楼层信息显示，显示模块由一位数码管以及两个方向显示数码管构成，考虑到各个楼层的显示信息都是一致的，故只需要设计同一个信号输出端口即可。此外考虑到在设计中000表示第一层，100表示第五层，从人性化角度上应该做出如下转换：

| FLOORC~FLOORA | LEDC~LEDA |
| --- | --- |
| 000 | 0001 |
| 001 | 010 |
| 010 | 011 |
| 011 | 100 |
| 100 | 101 |

电梯运行方向的显示真值表如下：

| RUN  | DIR  | UP | DOWN |
| ---- | ---- | ---- | ---- |
| 0 | X | 0 | 0 |
| 1 | 0 | 0 | 1 |
| 1 | 1 | 1 | 0 |

电路设计如下所示：

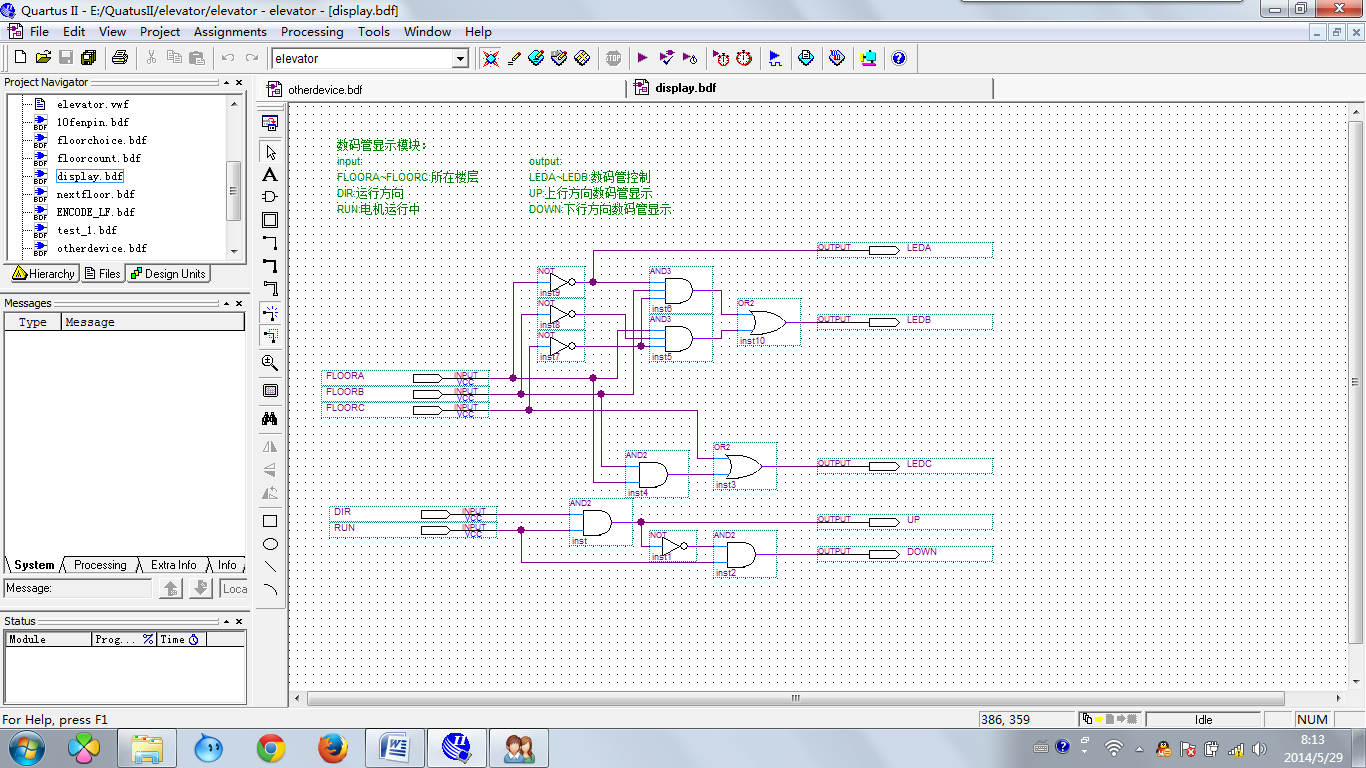
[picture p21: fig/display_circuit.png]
display_circuit


### 整机电路设计以及原理说明

#### 整机电路设计

根据第一节的系统设计框图将各个模块根据设计逻辑连接到一起，整体电路如下图所示：

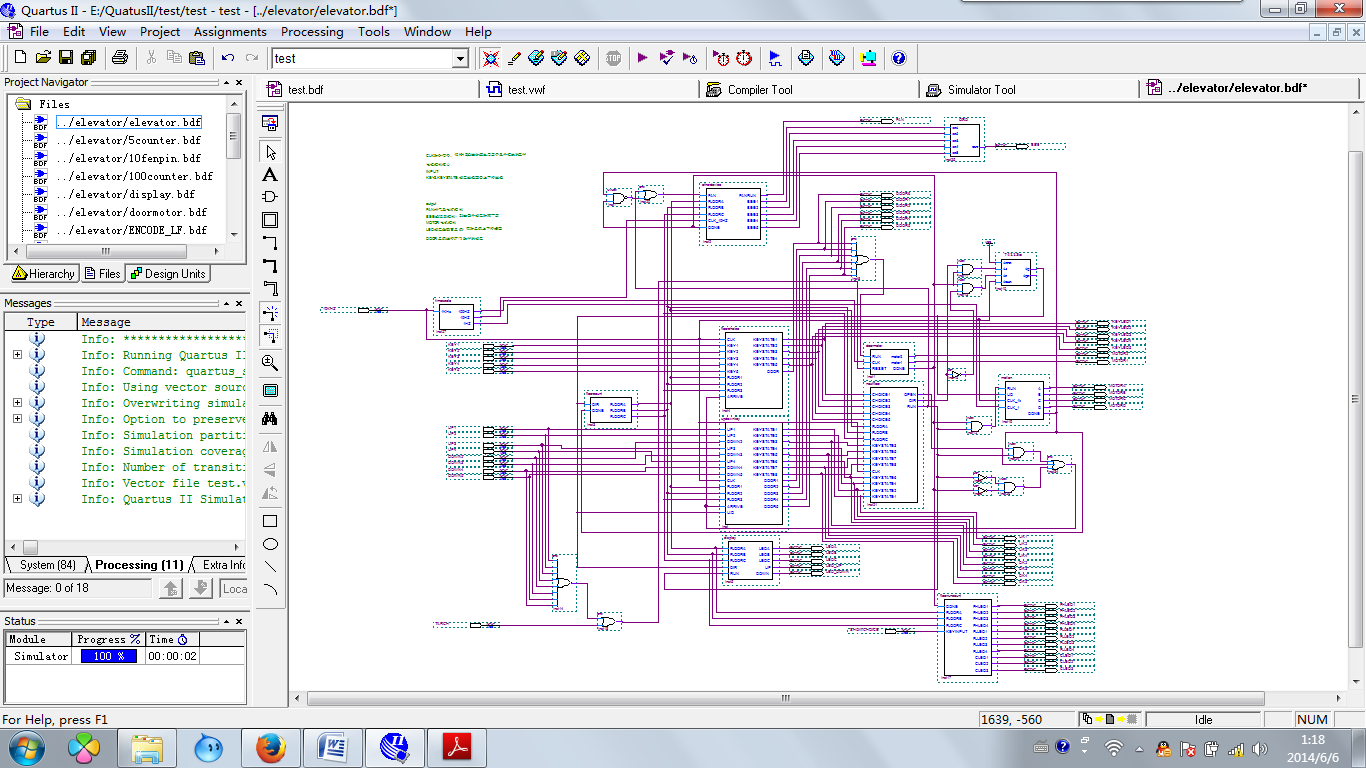
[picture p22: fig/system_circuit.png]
system_circuit


#### 原理说明

由于每个模块都各司其职，在第二节的设计中经过功能仿真保证了模块的功能实现。将各个模块的输入输出口对应相连即可实现第二章需要的功能。其中时钟模块输入为10KHz，输入各个频率信号到各模块，楼层计数模块输入信号为电梯轿厢电机运行结束的跳变信号，输出跳变之后的楼层信号到其他各个需要楼层信号的模块。此外核心决策模块，nextfloor主要根据按键的情况输出决策：RUN/DIR/OPEN 控制门电机以及轿厢电机的运行。因此将这些输出端口作为相关模块的输入。

### 性能测试及其结果

#### 上下行按键测试

使用1KHz 的时钟信号，设置如下输入信号：

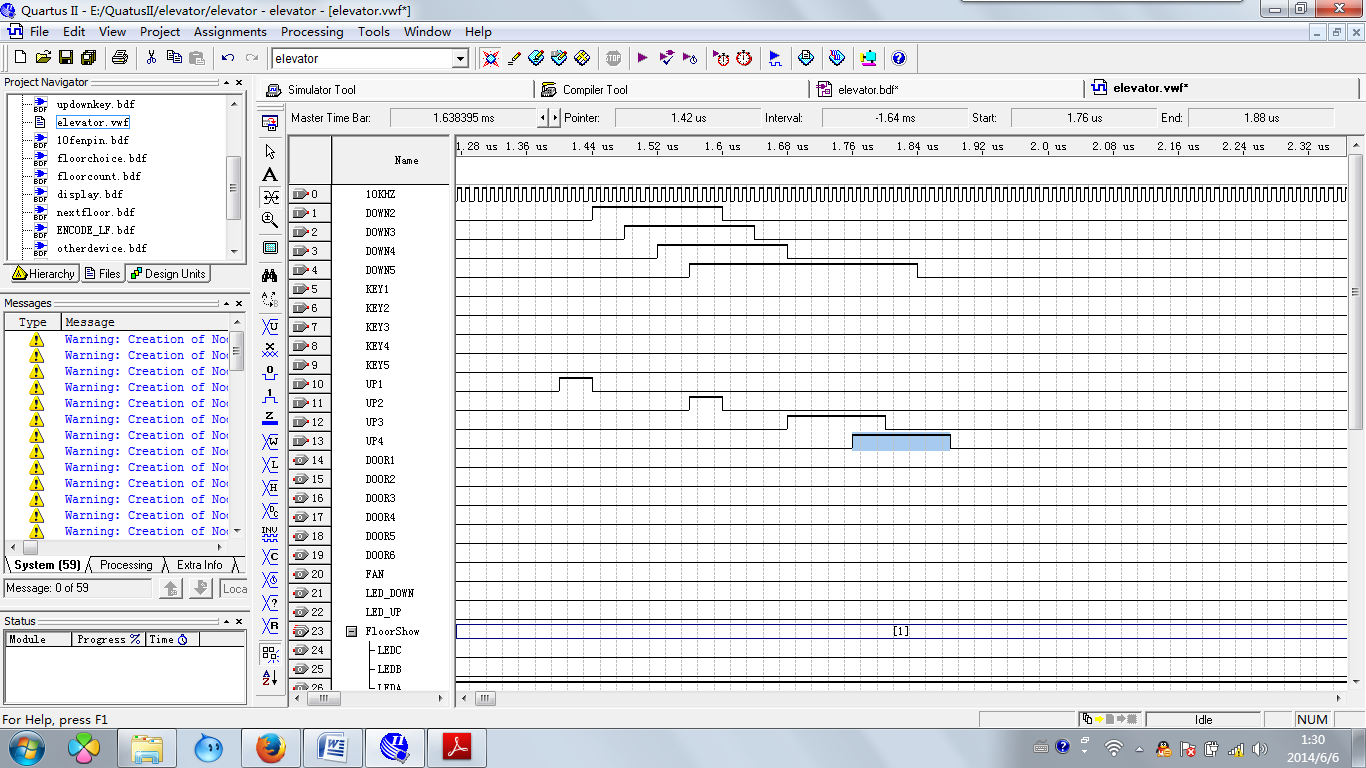
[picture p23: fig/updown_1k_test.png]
updown_1k_test


根据实际电梯运行的逻辑，由于首先按下的是上行按钮，故电梯在一楼会先开门，然后由于在开门过程中一次接收到来自DOWN2、DOWN3、UP2、DOWN4、DOWN5、UP3、UP4 的上下行按键信号，由于这些按键按下都是在电梯处于一楼开门过程发生的，因此电梯会对这些信息按照上下行的方向进行排序。一楼为上行优先，故排序结果为UP2、UP3、UP4、DOWN5、DOWN4、DOWN3、DOWN2，这意味着电梯会一次从一楼运行到五楼，再从五楼运行到二楼停止，在这过程中每一层楼都会开门一次，而且每次开门都会有一个提示音响起。

在电梯运行结束之后，保持运行方向的数据不变，电梯内的排气以及照明关闭。逻辑运行仿真图如下所示：

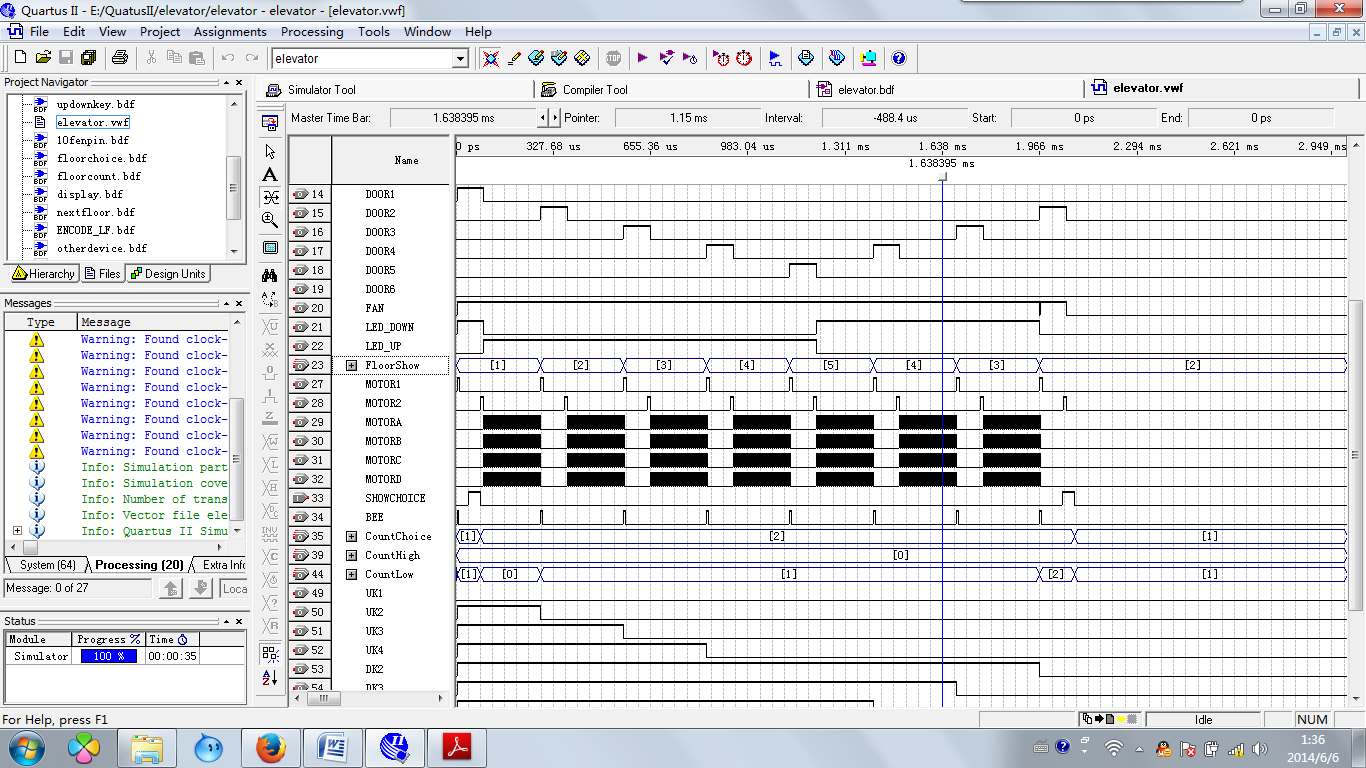
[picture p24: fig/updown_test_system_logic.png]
updown_test_system_logic


可见整个电梯运行逻辑符合现实运行的逻辑顺序。此外由于电梯在整个过程中在二楼开门次数为2 次，故根据楼层计数显示，二楼的计数次数为2次。而在楼层次数显示的选择按钮按下之前，系统显示的是1 楼的数据，开门之后一楼的运行次数为1.选择按钮按下之后，显示跳变为二楼的次数，此时为0 次；

#### 情景模拟测试

初始状态下电梯停靠在一楼，并且电梯门关闭。此时在2 楼有人按下上行按键打算去五楼，而在他按下之后在4 楼有人按下下行按键打算去一楼，模拟输入如下所示：

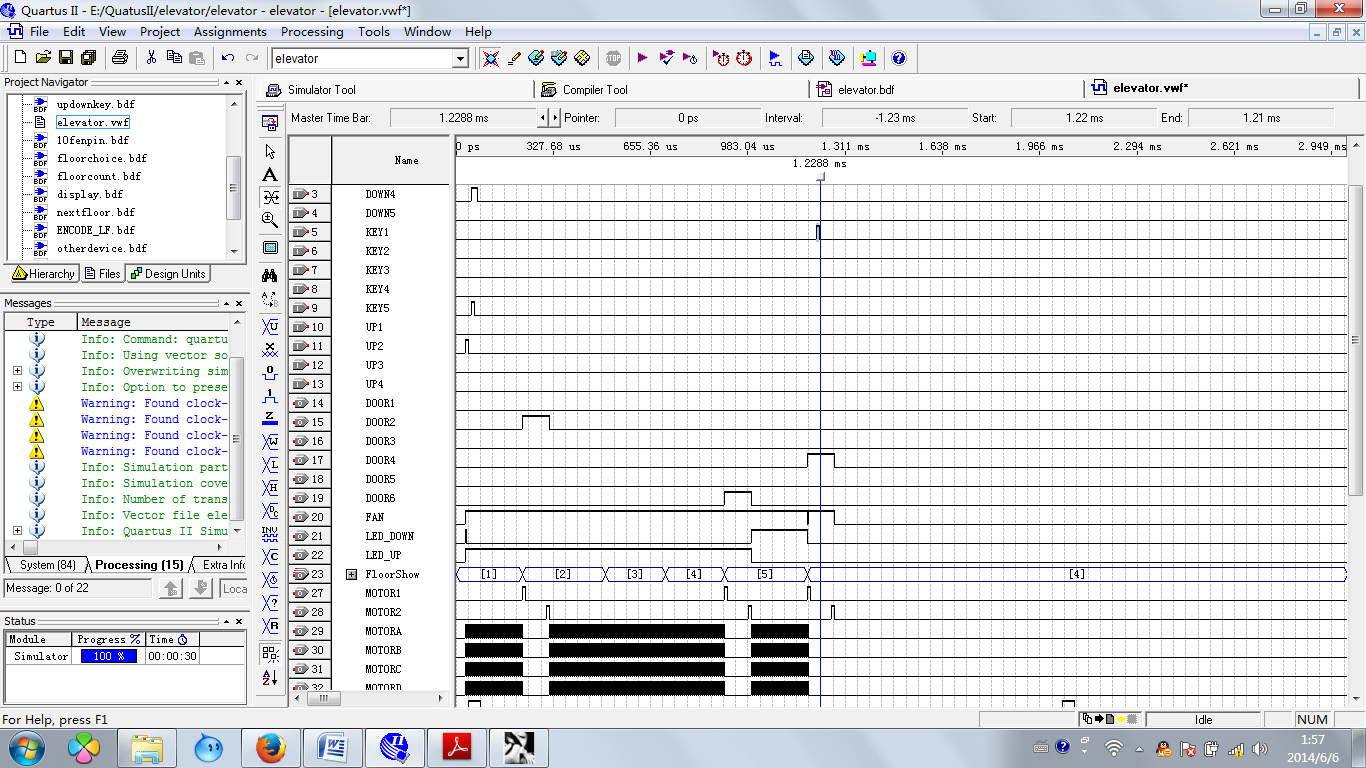
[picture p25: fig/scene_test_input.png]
scene_test_input


根据实际的运行逻辑，电梯在一楼不开门直接上行到二楼并开门，进入到电梯之后按下五楼的选择按键，在这过程中恰好四楼有人按下下行按键。电梯开始上行到五楼，进行开门动作，之后电梯下行到四楼开门，人进去之后按下一楼运行按键，电梯运行到一楼之后开门并停止。在楼层计数方面，先不输入选择信号，此时显示的是1 楼运行次数。根据设计原理，1楼的运行次数在电梯在一楼开门之后为由0 变为1。此后保持不变。

仿真结果如下，在该输入信号之下系统可以实现符合现实逻辑的输出。

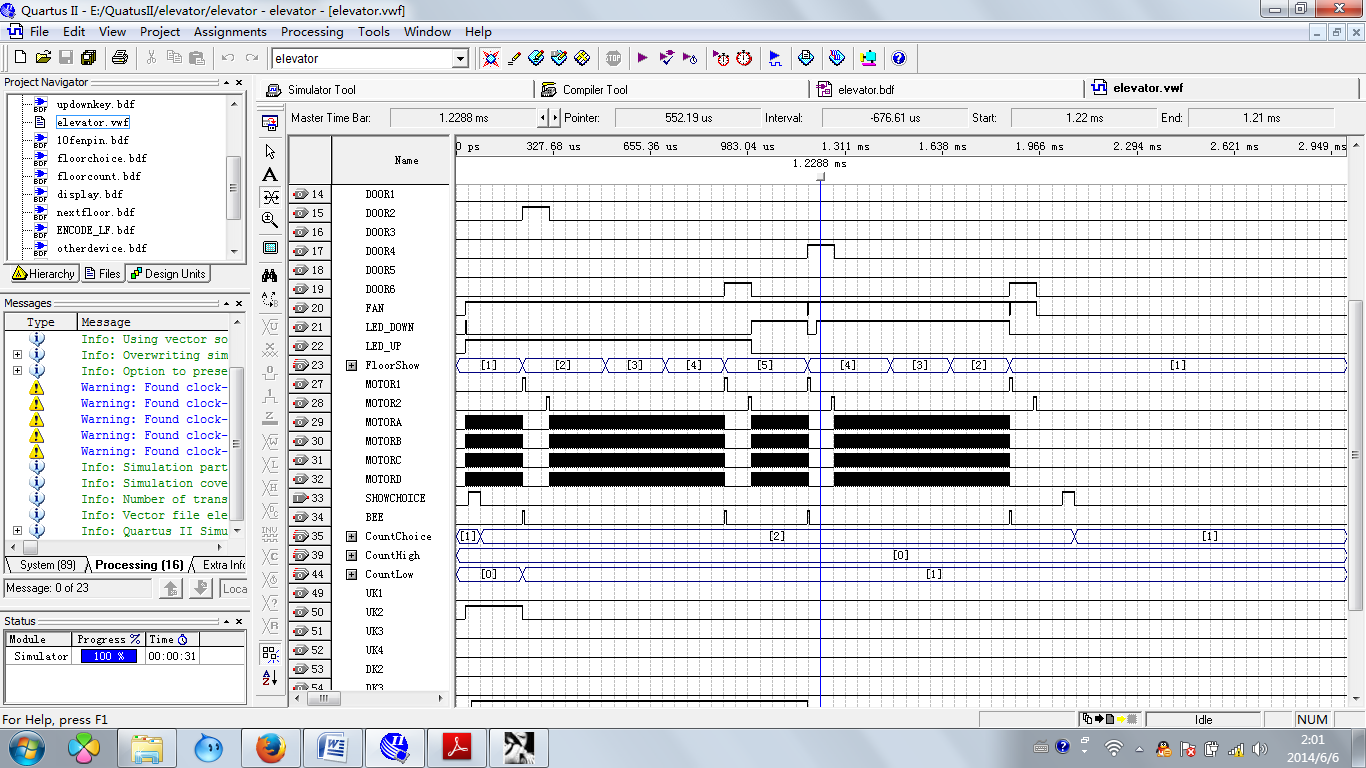
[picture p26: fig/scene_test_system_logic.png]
scene_test_system_logic


### 遇到的问题以及解决方案

#### 模块化编程的问题

由于刚接接触QuartusII 软件的设计，对模块化设计还是比较陌生的。但由于之前用c 语言编程的时候习惯用h 文件对各个子程序进行模块设计故在开始本次电梯设计的时候便碰到如何使用该软件进行模块设计的问题。

在查阅了相关资料之后总结以下几点：

1. 设计流程：先建立BDF 文件进行电路设计，然后点击FILE 里面的Create Symbol File 即可生成该模块；
2. 各个模块需要功能明确，模块名称以功能命名；
3. 每个模块都有两个文件，包括bdf 以及bsf两个文件，这样两个文件的名称一定要一致，并且在设计完成之后不可删除bdf 文件，否则模块会出错；

#### 仿真时间的设置

一般来说系统的仿真时间默认为1ms，所以在需要进行比较长的仿真就需要对系统的仿真时间进行修改。通过查阅资料可知具体操作为：点击EDIT菜单选择EndTime，将时间修改为需要的时间即可。

#### 输出端口的合并

在仿真的时候，如果具有很多的输出端口，便会对同步观察波形产生一定的困难。如果有一些端口，如表示楼层的三个端口，则可以将其合并显

示为10 进制的数。 

操作为：选择需要合并的端口，点击右键Group，并命名即可。这样会大大缩减端口量，也便于观察。

#### 关于Timing 跟Functional 仿真的区别

在仿真中一般选择Functional 进行仿真，有时错点为Timing 仿真之后波形图会变得出乎意料。主要原因是，Functional 仿真只是针对于功能的仿真，对时间要求不高。而Timing 仿真则是充分考虑了竞争冒险以及线延时等时间上的问题，故仿真的结果比较接近现实，更容易发现竞争冒险的问题。

#### 关于out of block的解决方案

由于所使用的模块为CPM240T系列的芯片，该芯片限制用户最多只能使用240个block，在设计的时候通过compile的filter中的report可以查询实际使用的资源情况，包括每个模块包含的block信息等。在本次电梯设计中，由于项目比较复杂，故到后来即使出现了一些bug也不能通过编程解决。出现的问题包括：在选择楼层计数模块中原来按照100计数的模块由于该out of block的原因退而选择了40进制计数，每个子模块减少2个JK触发器。此外，该电梯在设计本身存在一个bug，也就是在关门1s内按下按键时可以恢复开门状态。但在设计的时候统一设计为按下任意门按键即可开门，无论是哪个楼层。该问题的解决方案是通过把一个或门改为相应的多个与或门即可，但由于block的限制，未能付诸实施。在本次的电梯设计中，通过多次对模块的简化，最终使用block数量为238个，使用率达99%。

关于降低block的使用率有以下几个方法：

1. 降低IO口使用数量，由于QuartuesII本身具有很强的优化功能，故降低IO口的的使用数量可以有效的简化模块，使block使用率大幅度降低。例如原来使用200以上个block，但删除一个没必要的IO端口之后可以降低到100左右；
2. 降低JK触发器的使用，因为每个JK触发器在计算上是一个block，因此从理论上降低一个触发器也就减少了一个block，这也是个人将计数从100进制降低到40进制的原因。
3. 减少一些与或非门等门电路的使用，这个方法不一定凑效。因为系统本身优化的原因，有一些门电路实际上已经是被优化过了，存不存在其实没多大关系。但有一些没被简化过的，通过个人的简化可以降低block的使用。

#### 关于按键初始状态的说明

初始设计为按键默认为低电平状态，在按下的时候出现高电平，但是由于PCB设计的原因后来改为初始状态为高电平，按下时低电平有效。PCB设计原来考虑CPLD芯片的引脚在初始状态应该为低电平，但实际为需要接入上拉电阻才能作为按键输入。否则一直保持低电平状态，并不会变为高电平。但由于设计的错误，最终只能外接上拉电阻，导致按键初始状态为高电平，按下时由于引脚接地而变为高电平。因此，在硬件固定之后只能通过改软件的设计来适应。故在本文中提及的功能不变而各个模块会出现一些出入。特此说明。

### 附录

#### 设计文件中模块名称与对应的功能说明

| 模块名称 | 对应功能 | 备注 |
| --- | --- | --- |
| 10fenpin.bsf | 10分频电路 | |
| 100counter.bsf  | 100进制计数器 | |
| display.bsf | 轿厢以及电梯门口数码管显示 | |
| doormotor.bsf | 门电机控制模块 | |
| ENCODE_LF.bsf | 低位优先8-3编码器 | |
| floorchoice.bsf | 轿厢内楼层选择按键输入 | |
| keyinput.bsf | 按键输入模块 | |
| motion.bsf | 电梯轿厢电机控制模块 | |
| otherdevice.bsf | 蜂鸣器、排气、照明电路控制模块 | |
| timescale.bsf | 时钟输入模块 | 输入1KHZ，输出10、100、1KHZ |
| nextfloor.bsf | 电梯运行逻辑判断模块 | 判断是否运行、是否停层以及运行方向 |
| updownkey.bsf | 上下行按键输入模块 | |
| elevator.qpf | 整机电路 | |
| floorruncount | 楼层运行次数计数 | |
| 5counter | 5进制计数器 | |
| 10counter | 10进制计数器 | |
| 4counter | 4进制计数器 | |

#### PCB制板电路原理图

##### 整体电路原理

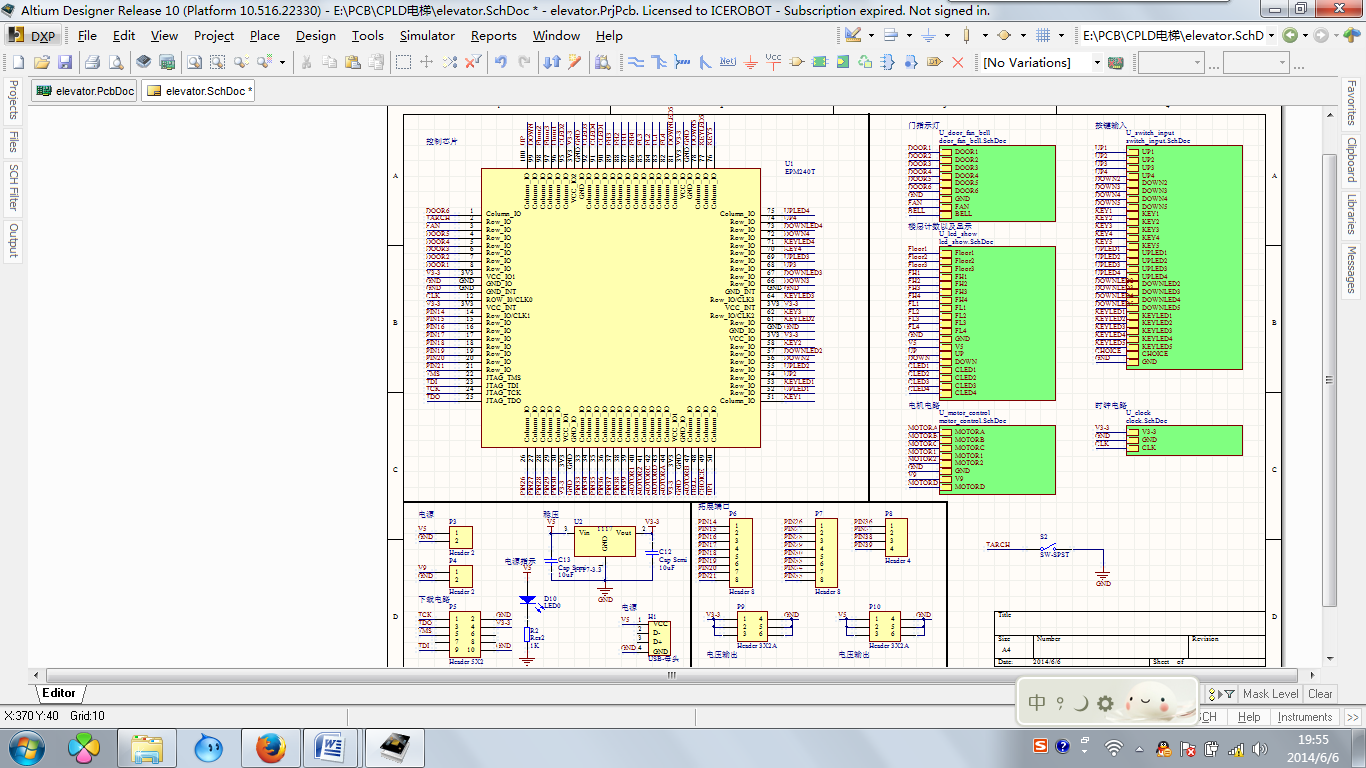
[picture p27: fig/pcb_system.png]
pcb_system


##### 时钟电路

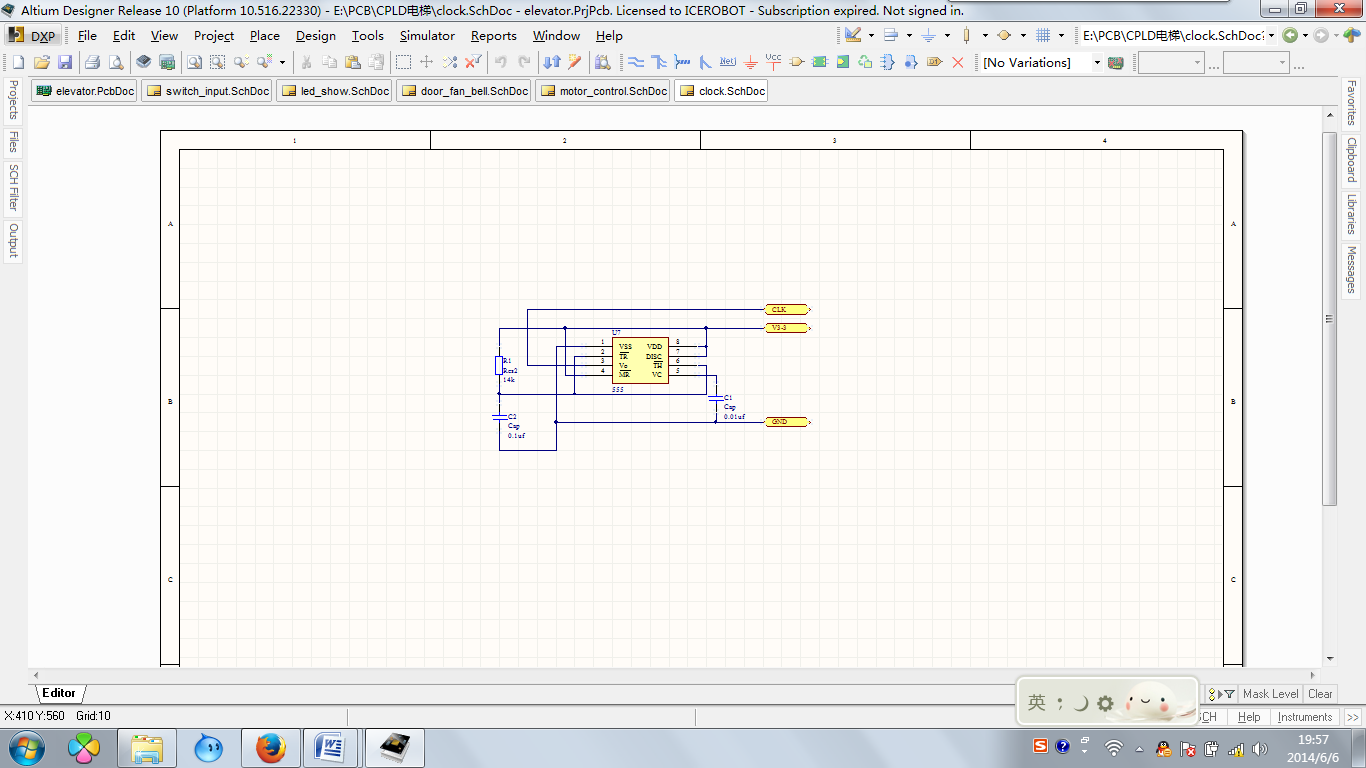
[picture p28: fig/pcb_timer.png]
pcb_timer


##### 电机电路

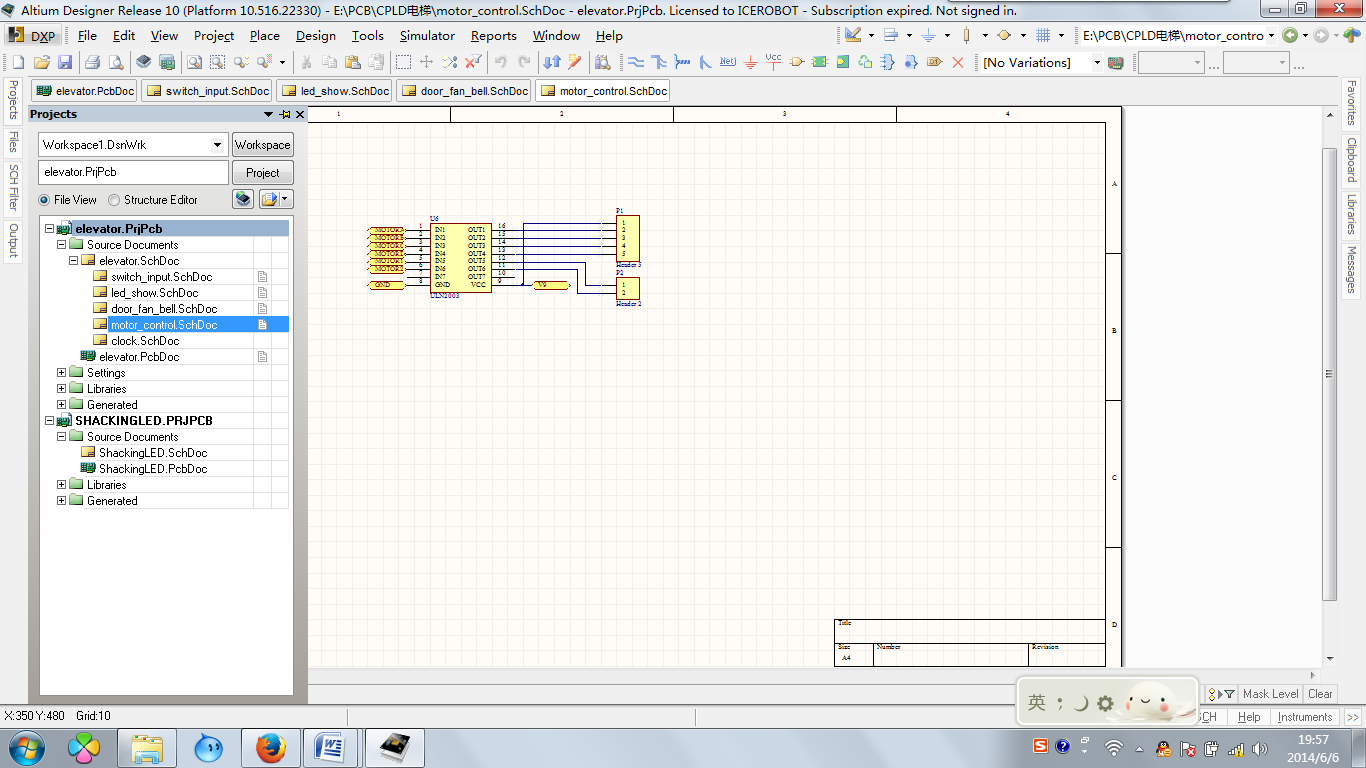
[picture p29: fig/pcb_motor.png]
pcb_motor


##### 按键输入

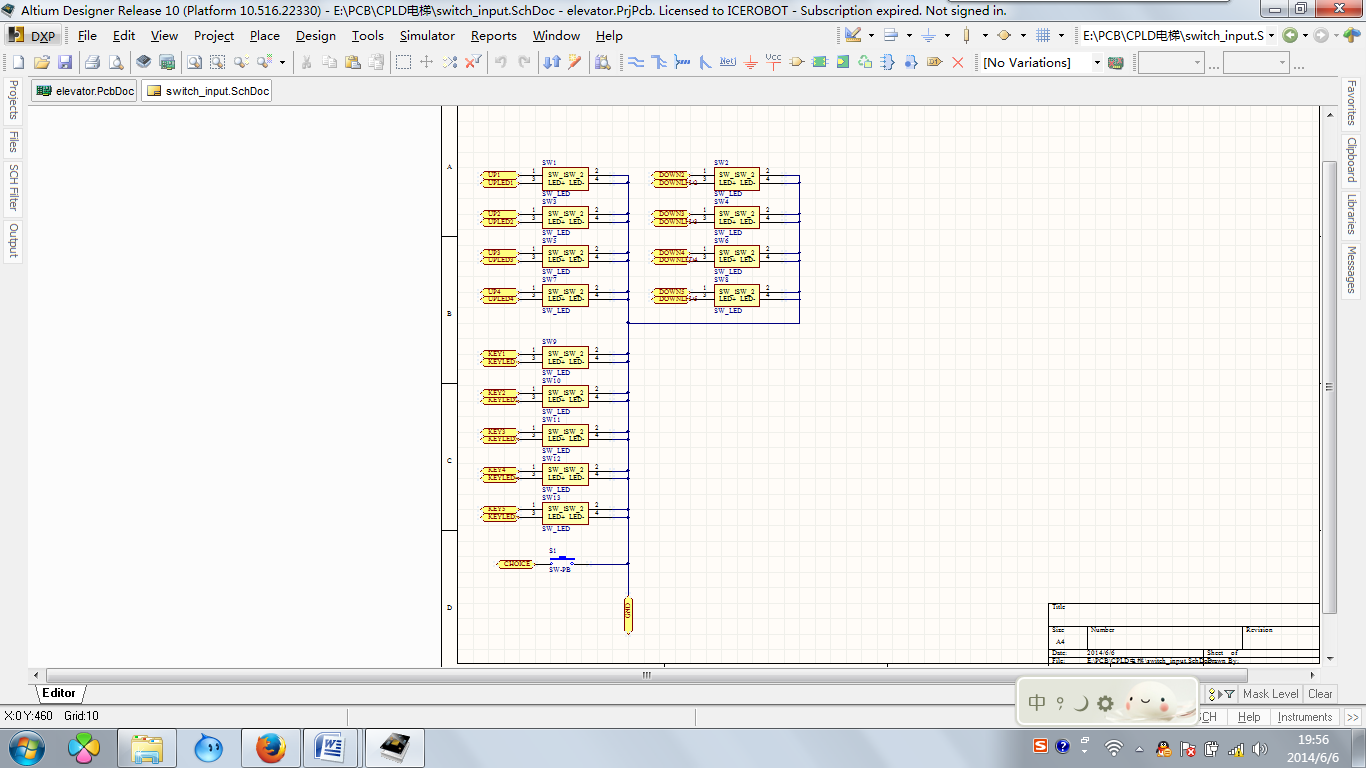
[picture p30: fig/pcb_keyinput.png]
pcb_keyinput


##### 数码管显示

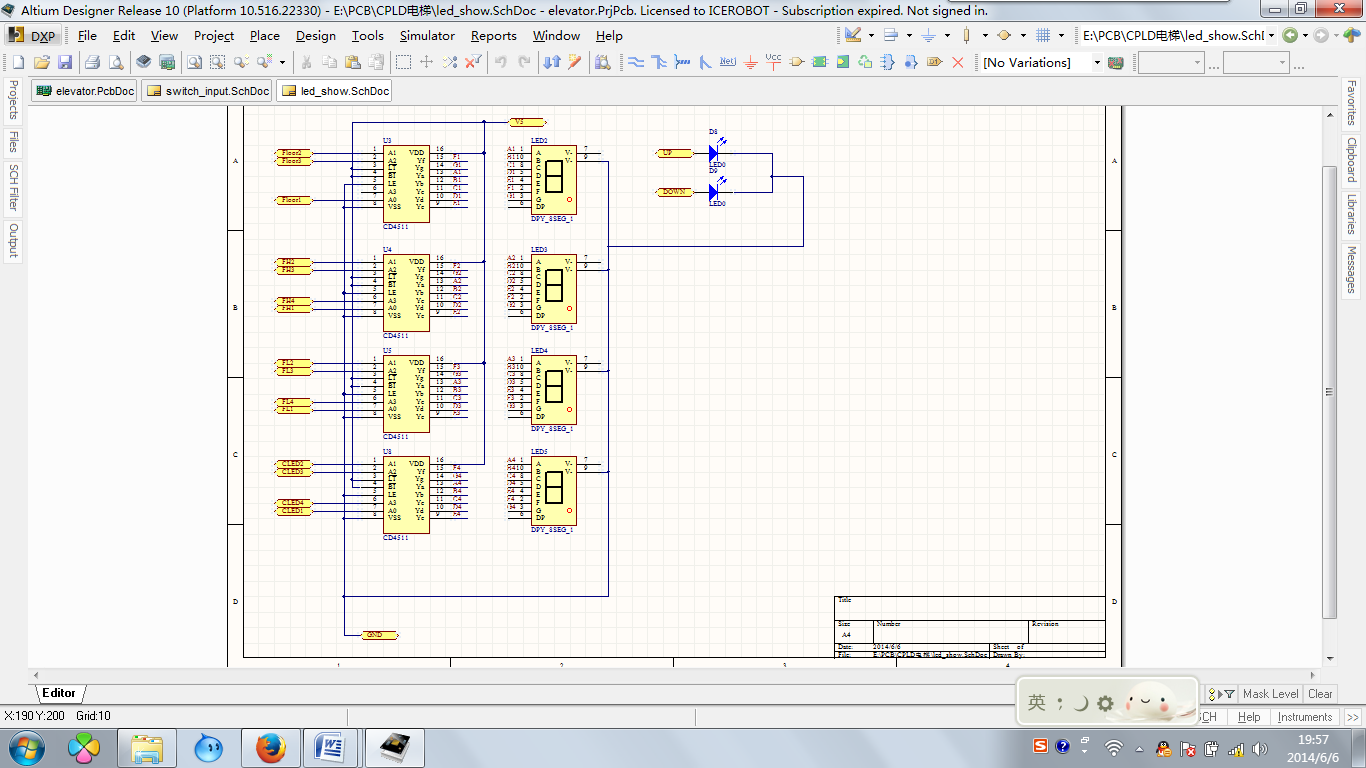
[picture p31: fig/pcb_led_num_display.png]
pcb_led_num_display


##### 楼层指示及蜂鸣器

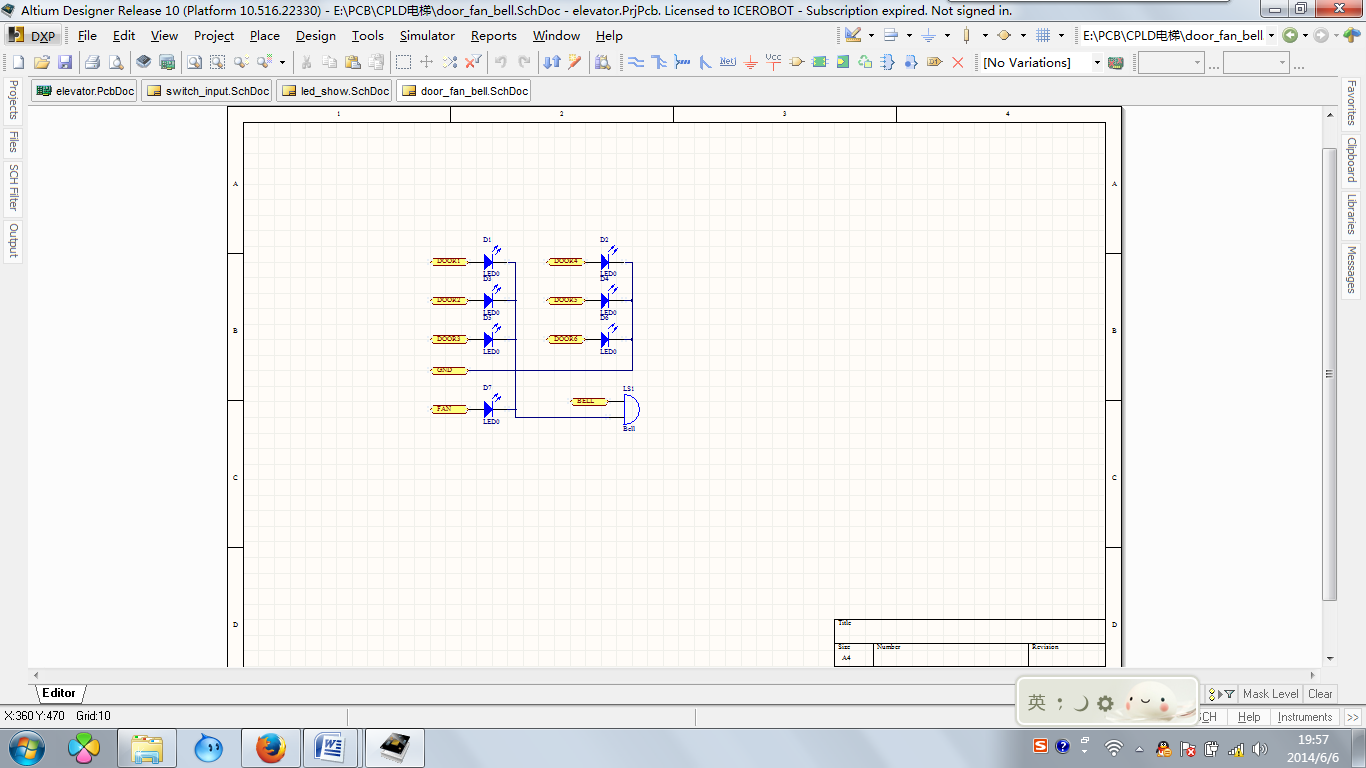
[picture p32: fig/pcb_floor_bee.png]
pcb_floor_bee


#### PCB布线图

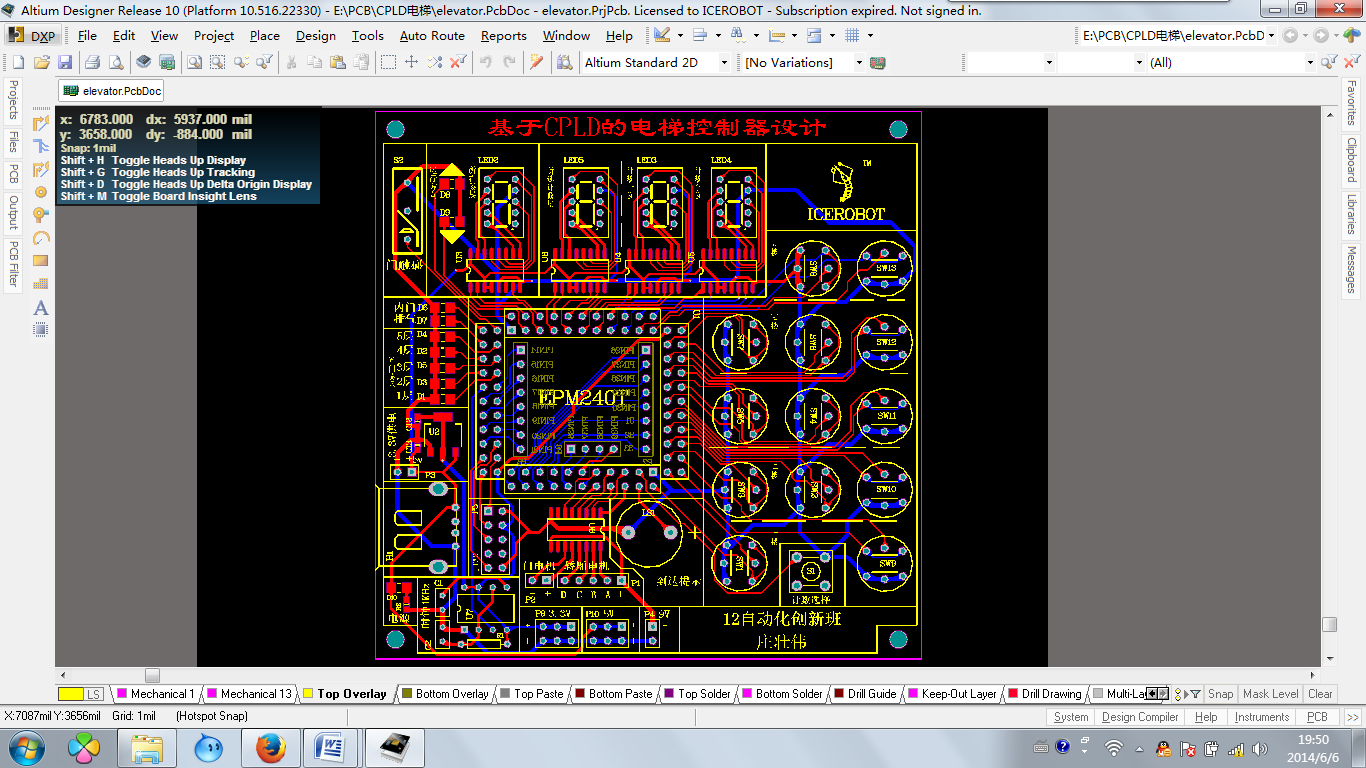
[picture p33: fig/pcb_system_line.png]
pcb_system_line


#### 样板测试

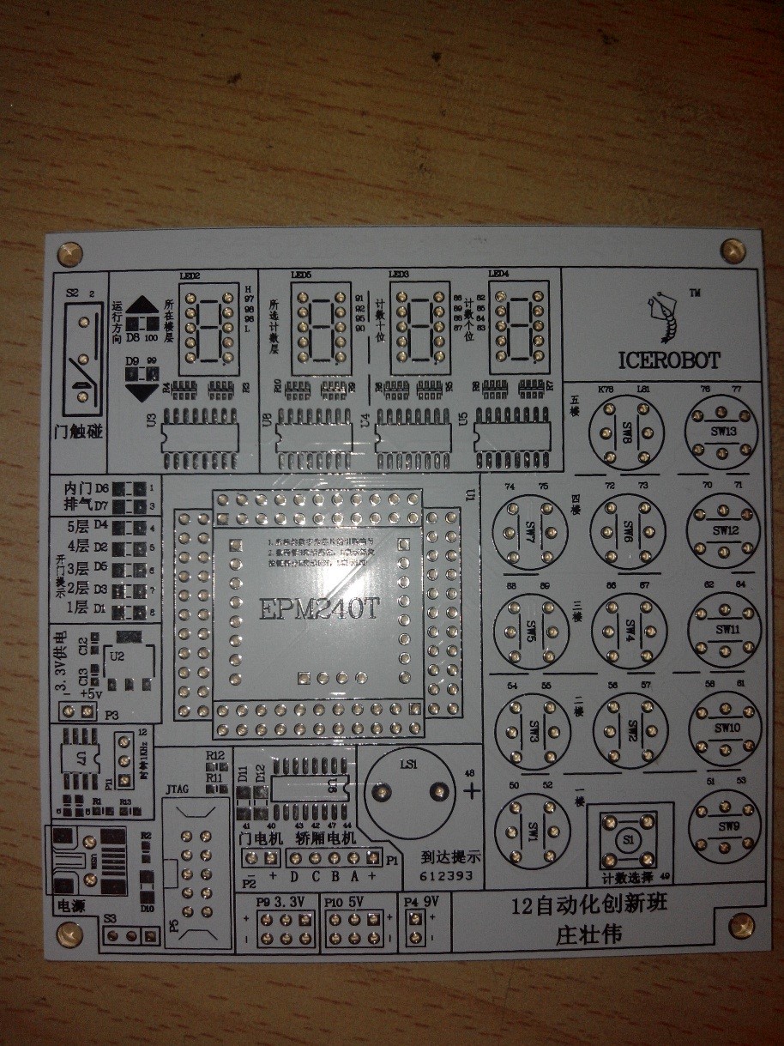
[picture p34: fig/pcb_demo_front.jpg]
pcb_demo_front


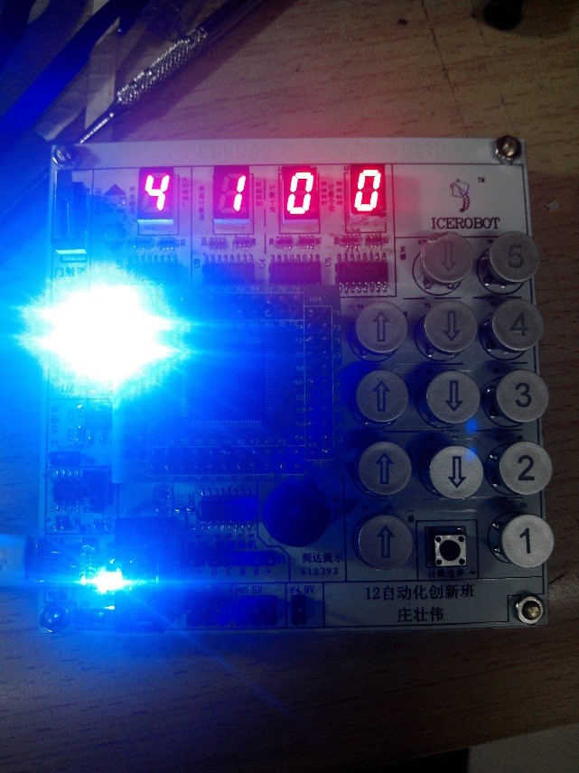
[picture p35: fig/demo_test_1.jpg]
demo_test_1


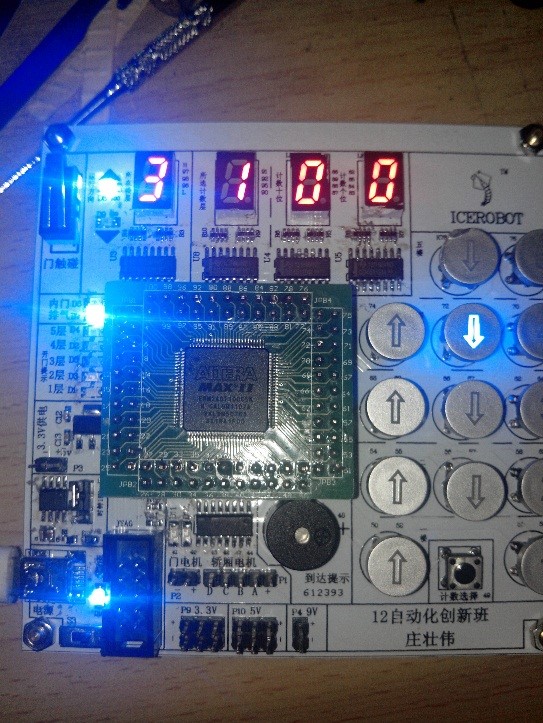
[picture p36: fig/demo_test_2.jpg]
demo_test_2


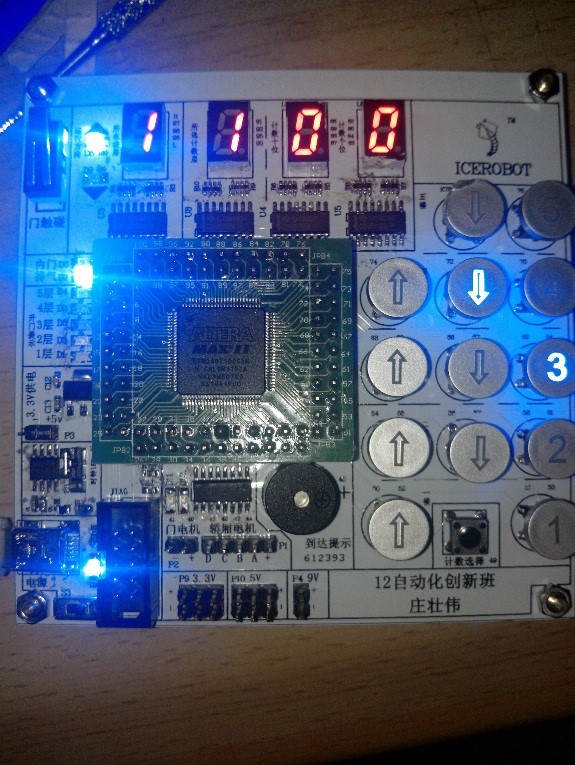
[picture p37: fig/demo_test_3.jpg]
demo_test_3


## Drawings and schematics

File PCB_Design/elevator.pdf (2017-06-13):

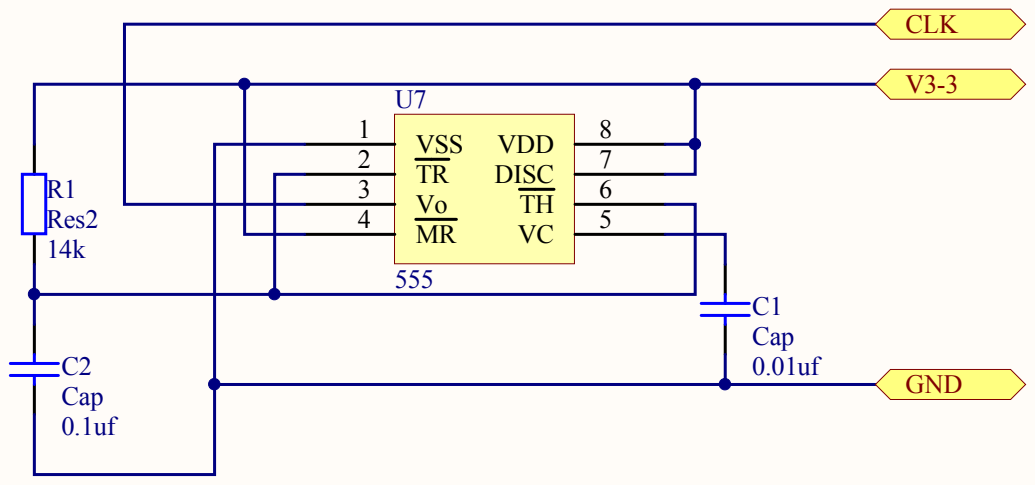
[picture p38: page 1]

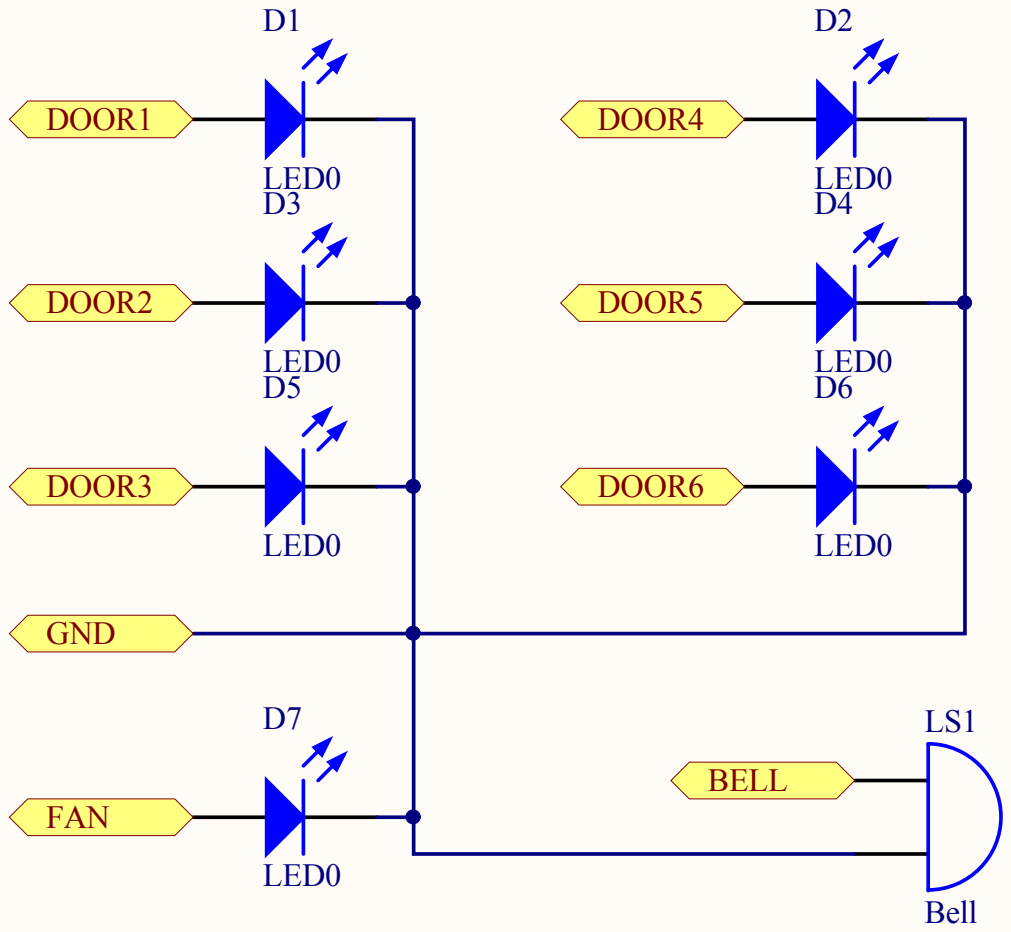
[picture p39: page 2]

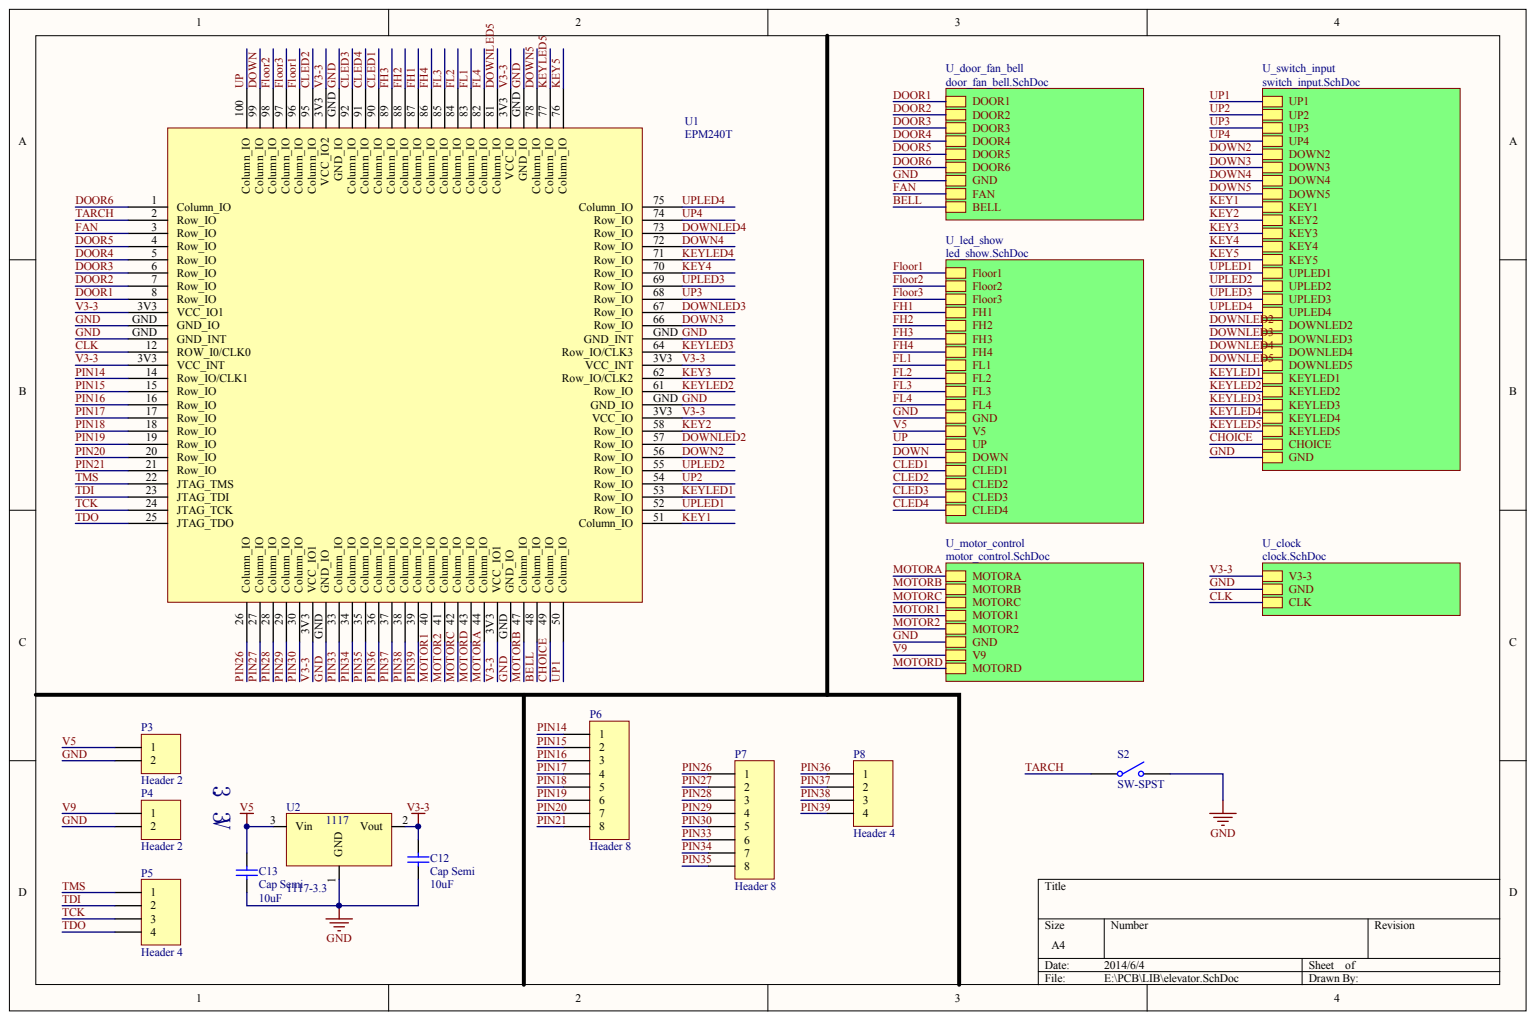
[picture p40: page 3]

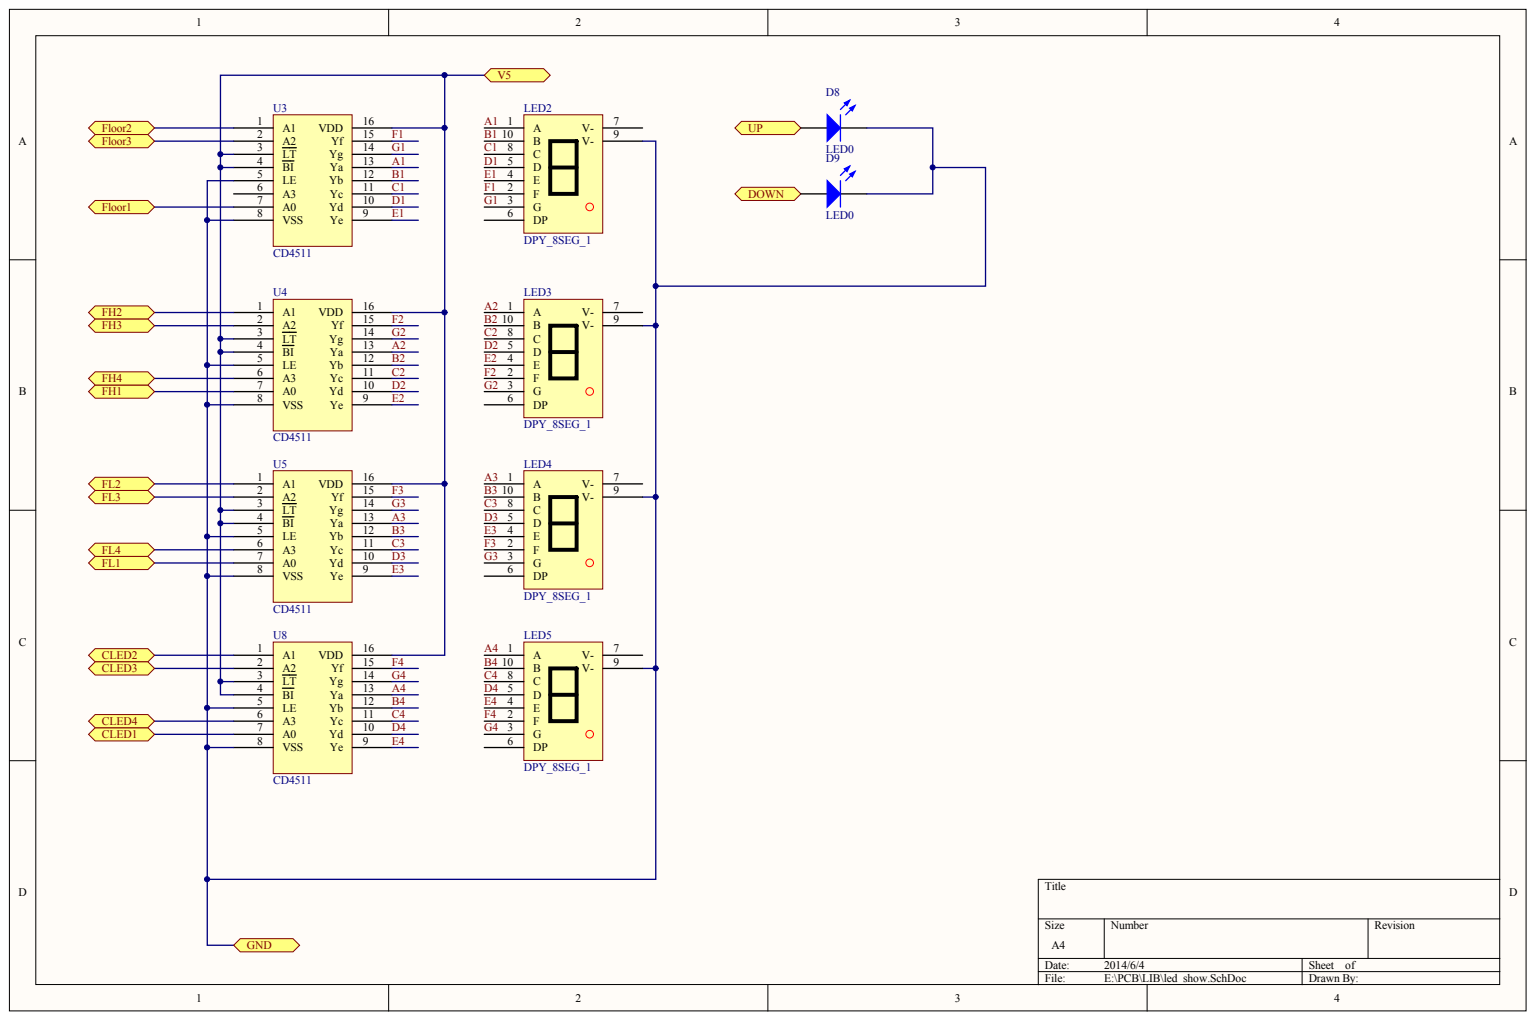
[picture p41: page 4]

BI 4 | | A1 B1 C1 D1 E1 | D1 | E 4 D 5
LE 5 | | | E1
A3 6 | | | F1 | F 2

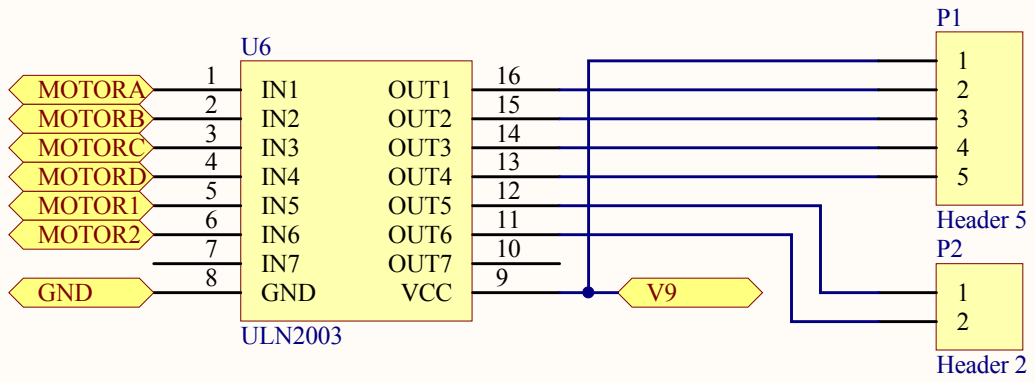
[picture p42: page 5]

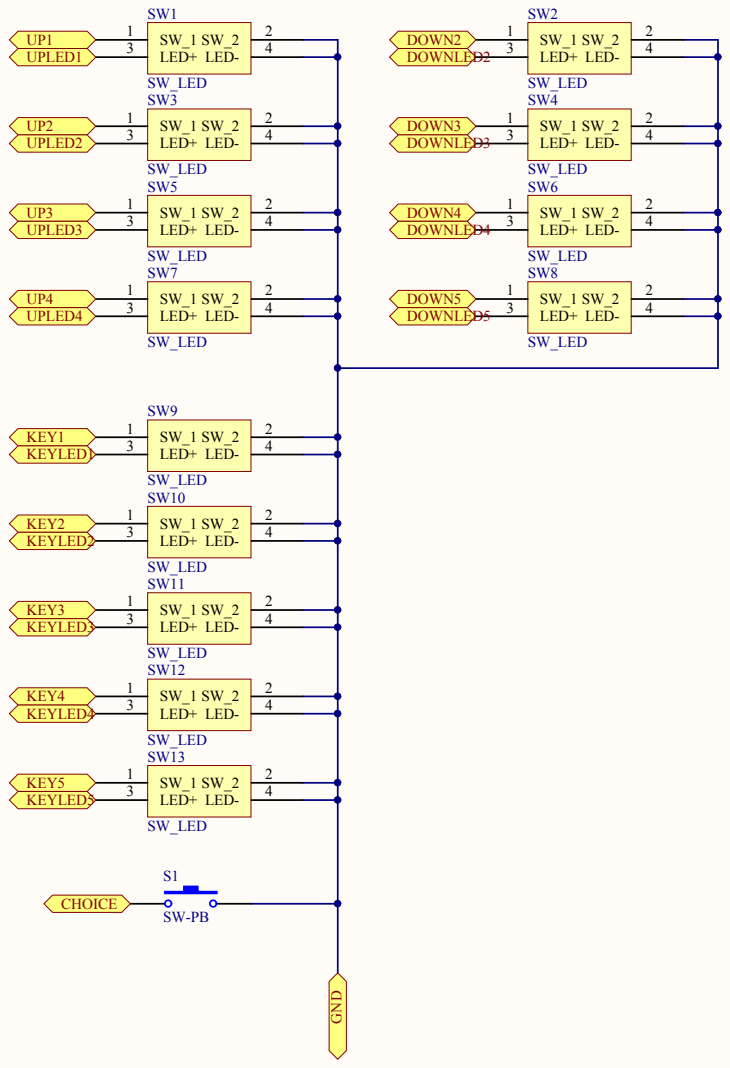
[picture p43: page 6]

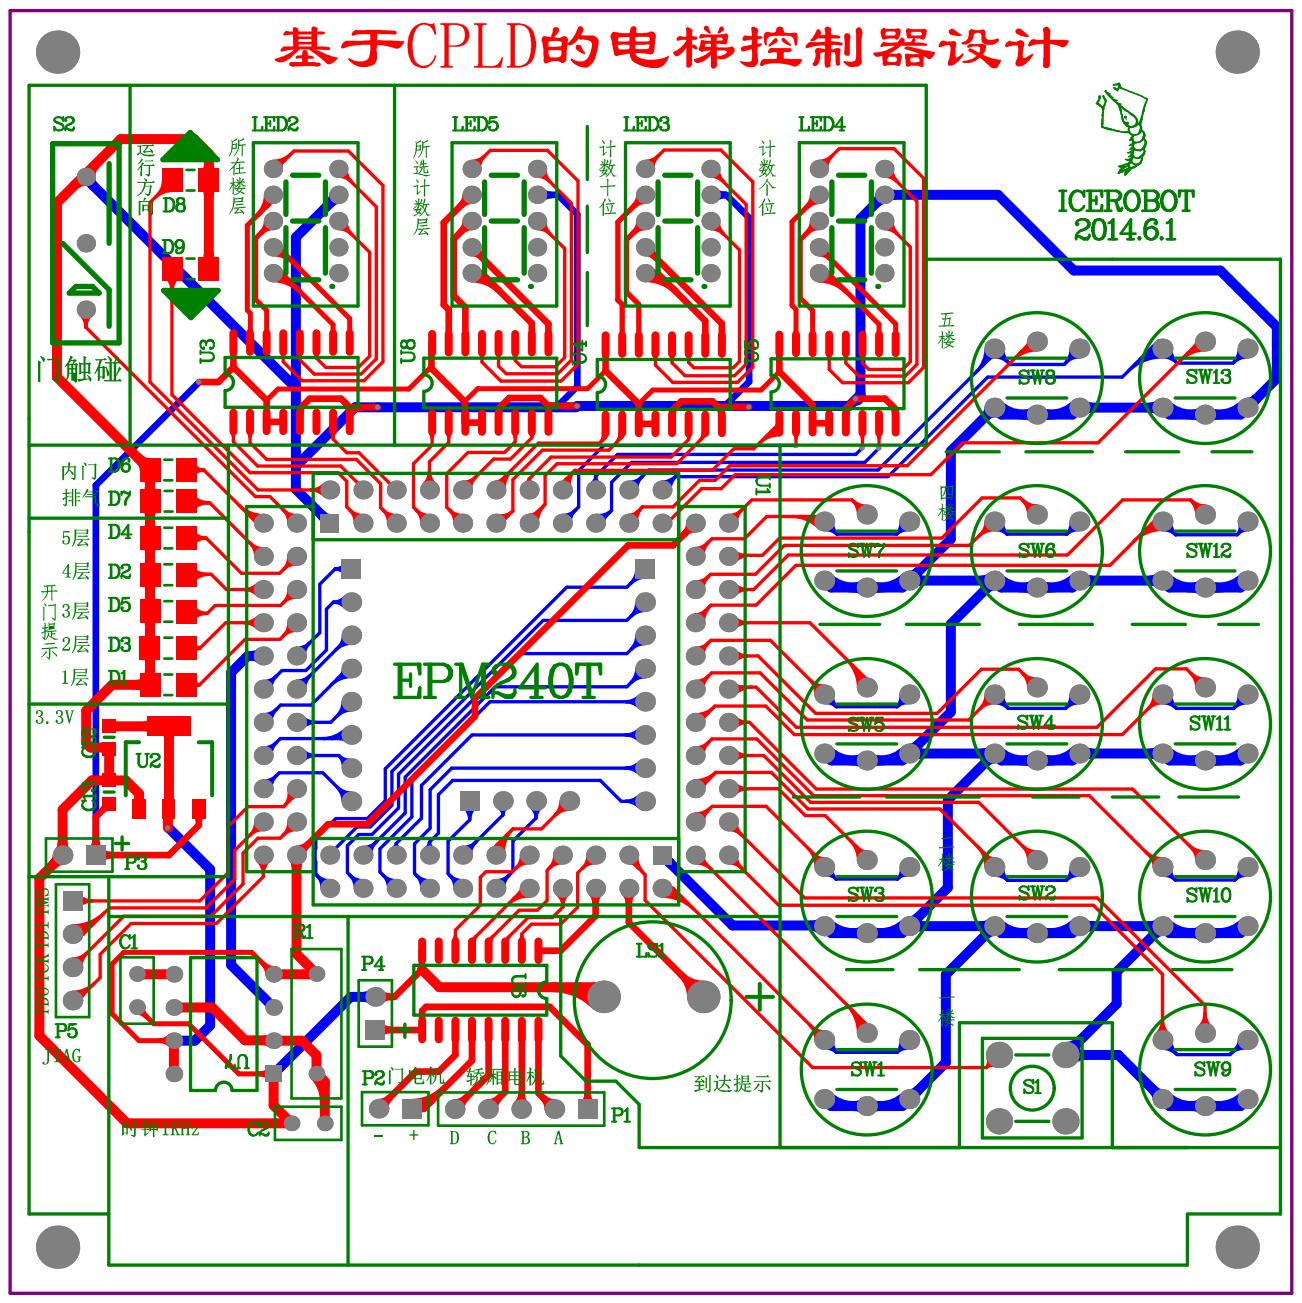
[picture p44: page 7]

Bill of Materials | <Parameter Title not found>
Source Data From: | elevator.PrjPcb
Project: | | elevator.PrjPcb
Variant: | | None
Creation Date: 2014/6/4 | 7:30:08
Print Date: | 41794 | 41794.31276
Footprint | Comment | LibRef | Designator | Description | Quantity
RAD-0.1 | Cap | Cap | C1, C2 | Capacitor | 2
0603 | Cap Semi | Cap Semi | C12, C13 | Capacitor (Semiconductor SIM Model) | 2
1206 | LED0 | LED0 | D1, D2, D3, D4, D5, D6, D7, D8, D9 | Typical INFRARED GaAs LED | 9
LED_SEG8 | DPY_8SEG_1 | DPY8_1 | LED2, LED3, LED4, LED5 | | 4
蜂鸣器 | Bell | Bell | LS1 | Electrical Bell | 1
HDR1X5 | Header 5 | Header 5 | P1 | Header, 5-Pin | 1
HDR1X2 | Header 2 | Header 2 | P2, P3, P4 | Header, 2-Pin | 3
HDR1X4 | Header 4 | Header 4 | P5, P8 | Header, 4-Pin | 2
HDR1X8 | Header 8 | Header 8 | P6, P7 | Header, 8-Pin | 2
RAD-0.3 | Res2 | Res2 | R1 | Resistor | 1
SW2 | SW-PB | SW-PB | S1 | Switch | 1
SW_TARCH | SW-SPST | SW-SPST | S2 | Single-Pole, Single-Throw Switch | 1
SW_LED | SW_LED | SW_LED | SW1, SW2, SW3, SW4, SW5, SW6,
| | | SW7, SW8, SW9, SW10, SW11, SW12,
| | | SW13 | | 13
CPLD100 | EPM240T | EPM240T1005 | U1 | 1
SOT-223 | 1117-3.3 | 1117B | U2 | 1
SOP-16 | CD4511 | CD4511 | U3, U4, U5, U8 | 4
SOP-16 | ULN2003 | ULN2003 | U6 | 1
DIP8 | 555 | NE555 | U7 | 1
| | | | 50
Approved | | Notes
